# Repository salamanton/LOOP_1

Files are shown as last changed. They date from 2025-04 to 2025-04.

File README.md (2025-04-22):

# LOOP_1
Step-by-step instructions to build an open-source recordplayer, that is upgradeable, repaireable and customizable to your needs.

Loop_1 is a do-it-yourself record player. Our goal with this object is to motivate people to deal with the return to analog. Since digitalization, music has become 
increasingly accessible. Platforms such as Spotify, AppleMusic or YouTube offer us a selection that far exceeds our expectations, which means that a profound examination of the music, the albums and the artists is becoming less and less possible. In order to promote a more conscious consumption of music, Loop_1 will expand the ritual of putting on records with a record player kit to build or rebuild yourself. 
kit to build or rebuild yourself in order to continue to ensure availability for young people interested in music or for nostalgics. 
nostalgics. At the same time, the record player will be used as a trend medium to further spread the topic of open source and make makerspaces more accessible to various communities.

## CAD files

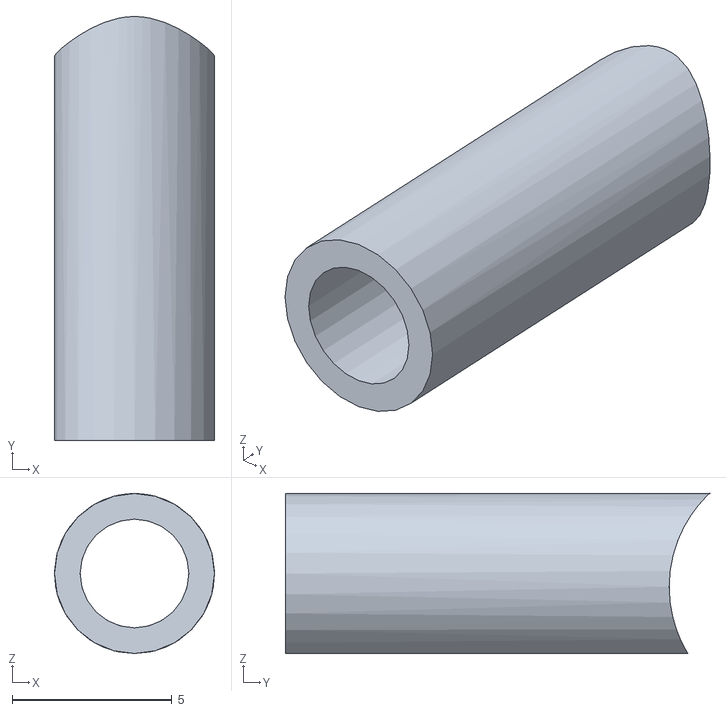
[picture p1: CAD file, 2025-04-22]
3D_Files/Distanzstück_arm_02.stl
5.00 x 13.3 x 5.00

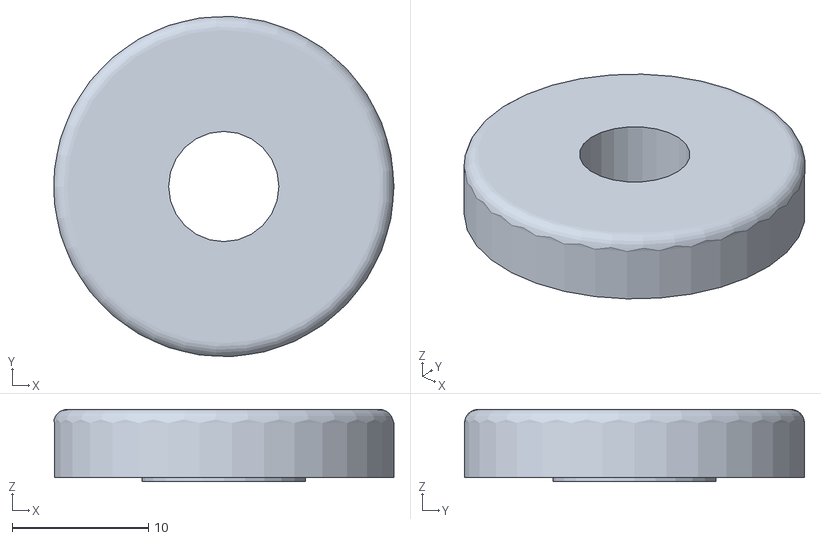
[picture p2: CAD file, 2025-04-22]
3D_Files/Anker_Abdeckung.stl
25.0 x 25.0 x 5.30

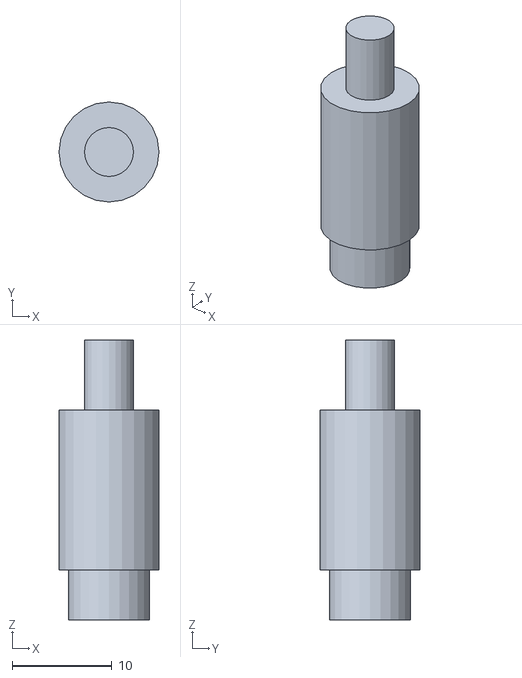
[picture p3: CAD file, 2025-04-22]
3D_Files/Distanzstück_02.stl
10.0 x 10.0 x 28.0

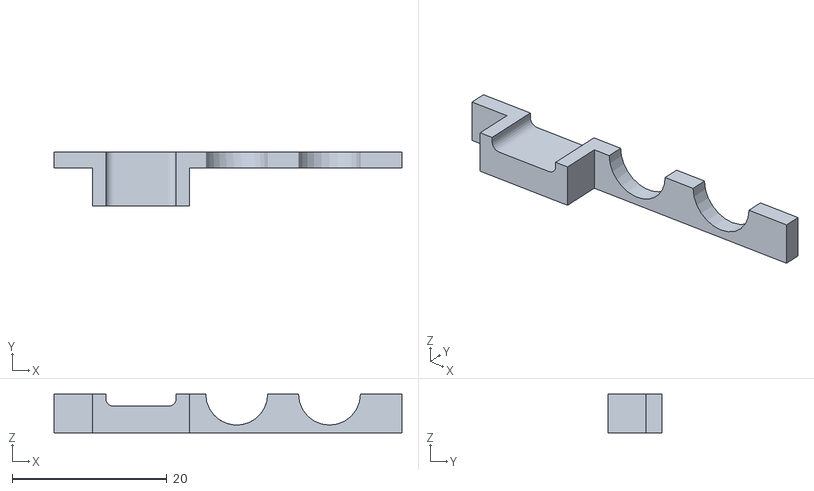
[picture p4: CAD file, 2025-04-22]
3D_Files/Ausgang_01.stl
45.0 x 7.00 x 5.00

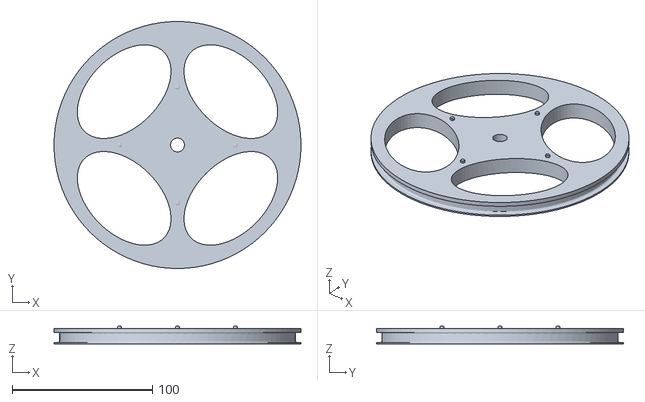
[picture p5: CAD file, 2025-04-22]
3D_Files/drehscheibe.stl
176.0 x 176.0 x 12.5

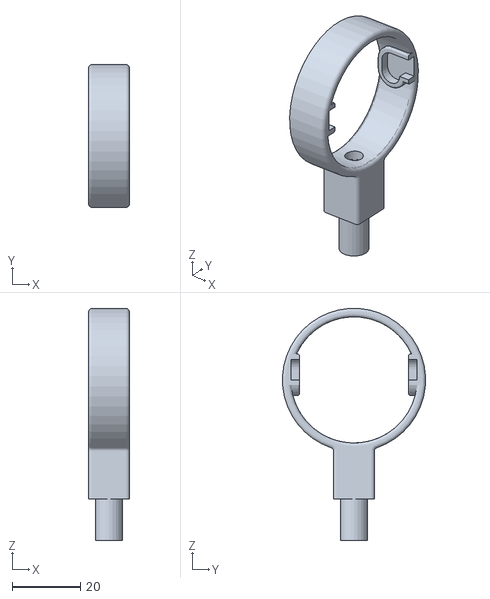
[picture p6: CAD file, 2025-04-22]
3D_Files/Anker.stl
12.0 x 41.9 x 68.0

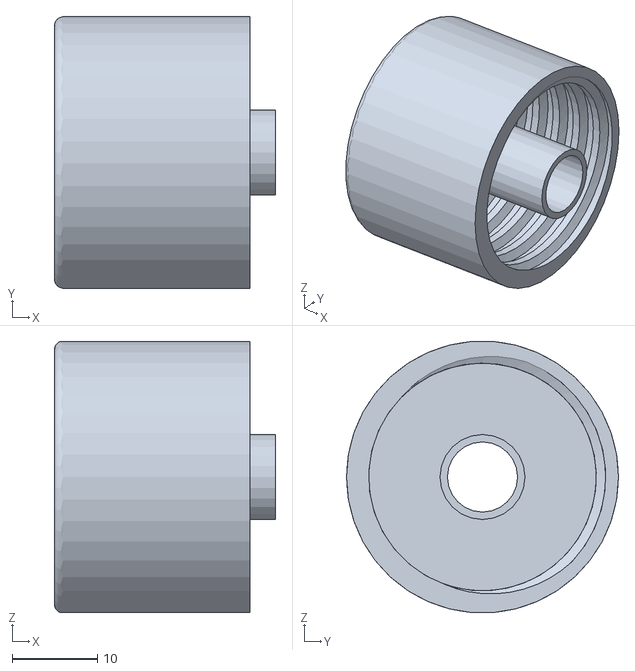
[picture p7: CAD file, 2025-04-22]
3D_Files/Gewicht_Gehäuse.stl
26.0 x 32.0 x 31.9

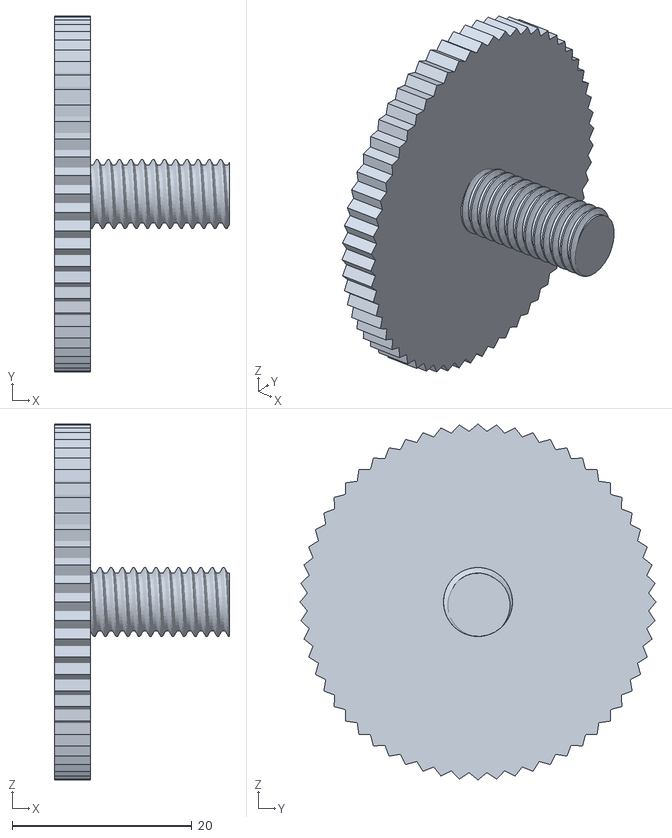
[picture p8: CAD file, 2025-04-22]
3D_Files/Stellschraube.stl
19.5 x 39.6 x 39.6

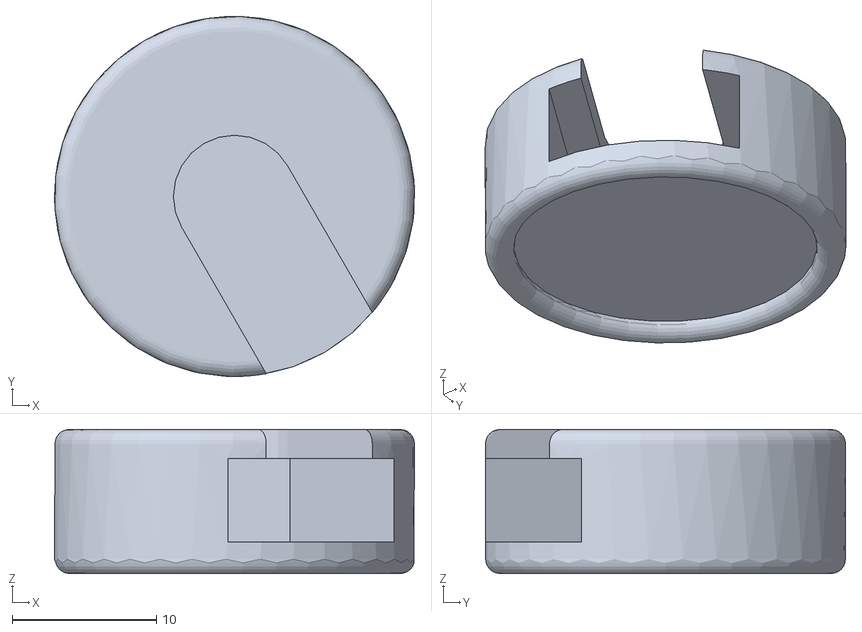
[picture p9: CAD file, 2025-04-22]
3D_Files/Fuß.stl
25.0 x 25.0 x 10.0

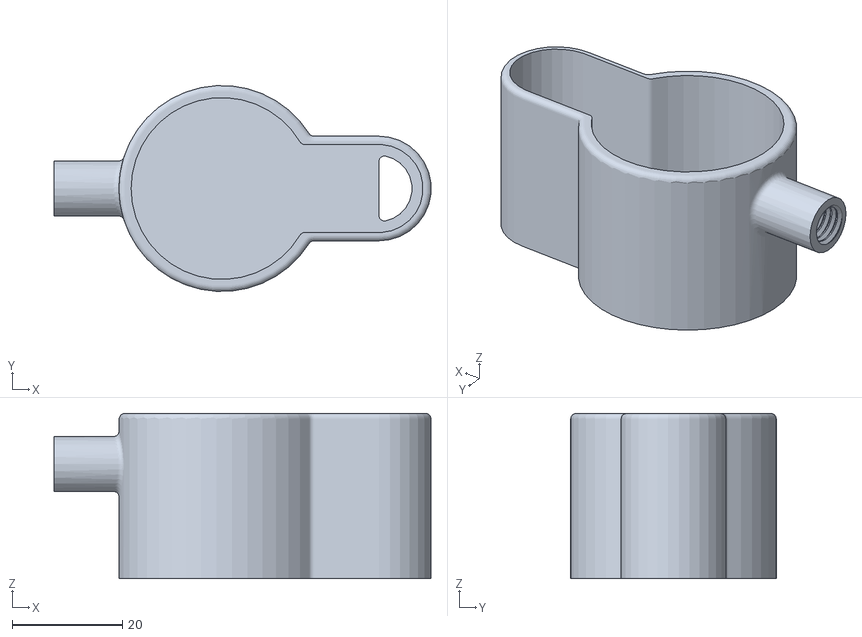
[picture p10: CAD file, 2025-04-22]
3D_Files/Schlitten.stl
68.4 x 37.3 x 30.0

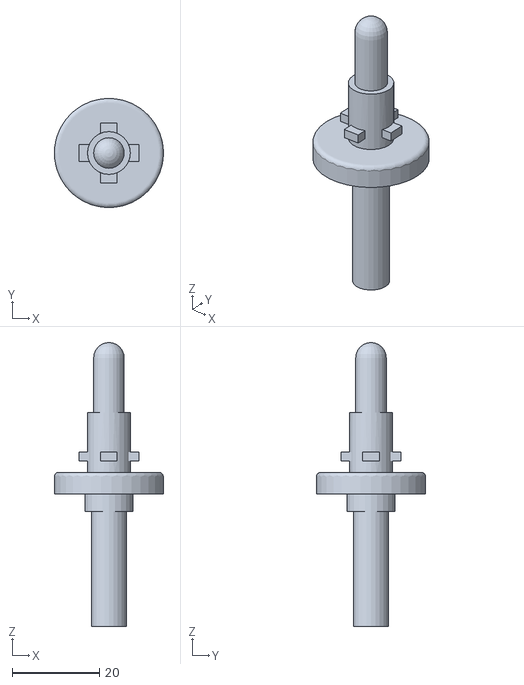
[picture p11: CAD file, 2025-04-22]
3D_Files/Achse.stl
25.0 x 25.0 x 65.0

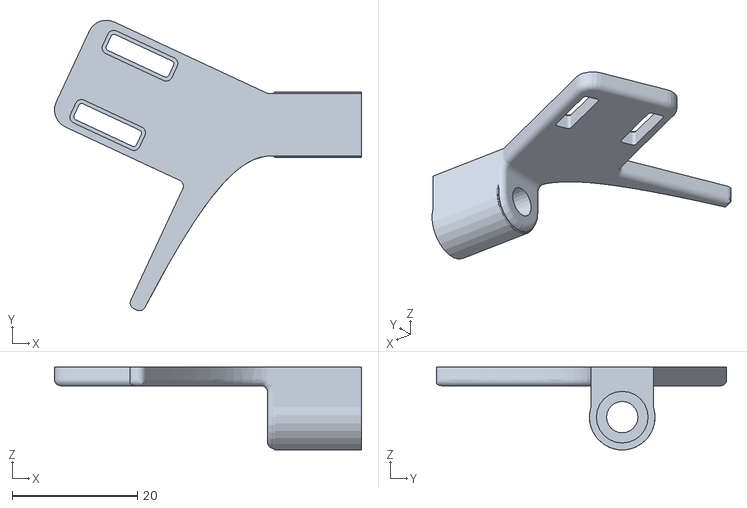
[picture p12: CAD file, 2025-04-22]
3D_Files/Tonabnehmer.stl
49.0 x 46.4 x 13.2

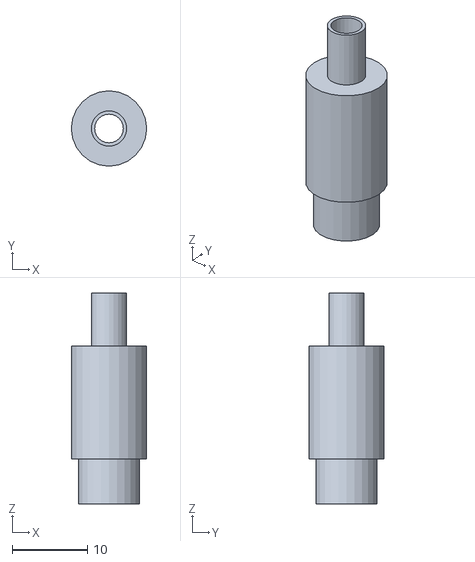
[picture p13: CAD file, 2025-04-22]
3D_Files/Distanzstück_01.stl
10.0 x 10.0 x 28.0

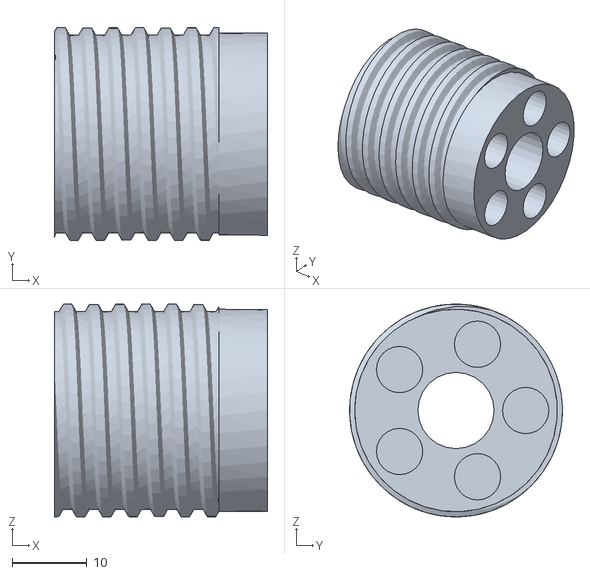
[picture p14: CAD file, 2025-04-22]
3D_Files/Gewicht_Halter.stl
28.5 x 28.5 x 28.5

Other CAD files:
3D_Files/Ausgang_02.stl
3D_Files/Distanzstück_arm_01.stl

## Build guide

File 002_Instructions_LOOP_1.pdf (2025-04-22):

# LOOP-1

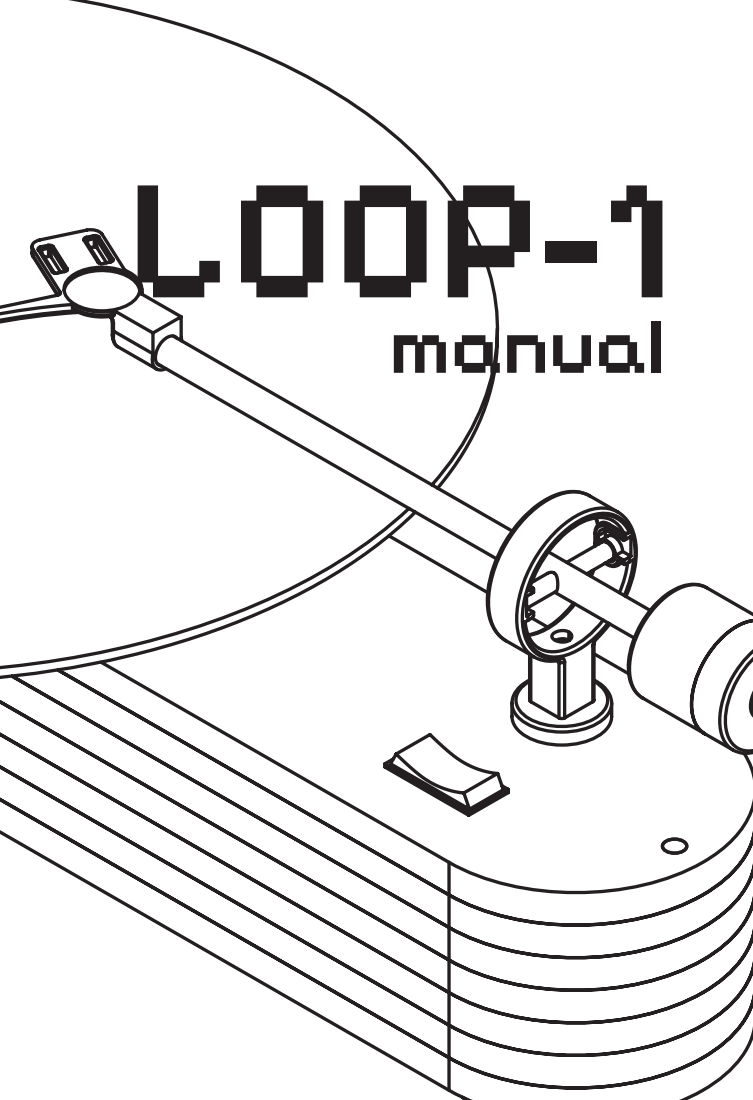
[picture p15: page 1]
manual

## Bill of materials

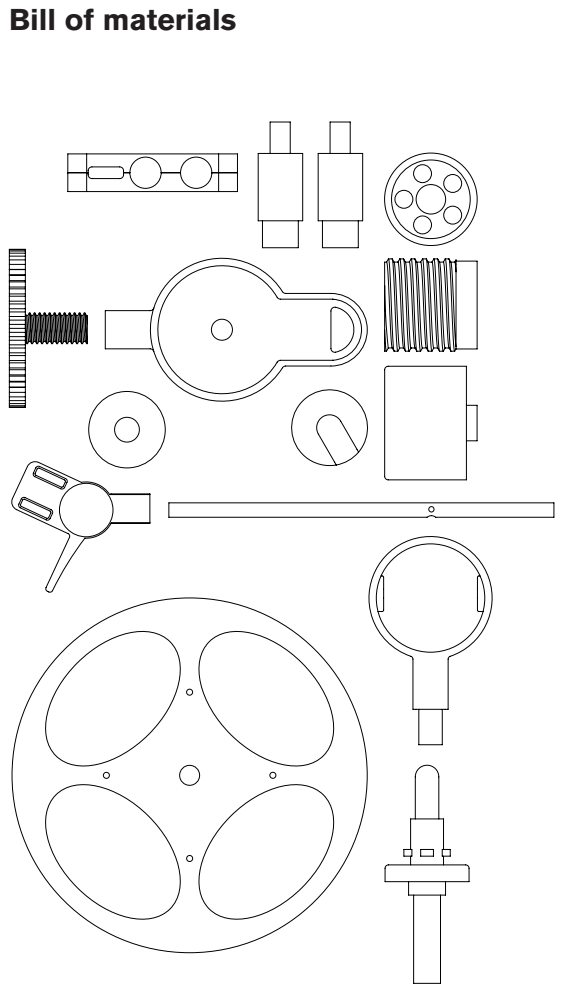
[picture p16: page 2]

Schrauben | Anzahl
M1 *4 | 8
M8 *20 | 4
Elektronik
Arduino Uno | 1
Motortreiber L298N | 1
Mini Breadboard | 1
Jumper Wire | 14
Cartridge Wire | 2
Phono Out | 2
Usb-C Port | 1
3-Positionen Kippschalter | 1
Phono Motor | 1
Spezial Komponenten
Kugellager 22mm | 4
Kugellager 6mm | 2
Stahlstab 30x3mm | 1
Stahlstab 70x6mm | 2
Stahlstab (Gewicht) 30x6mm | 5
Andere Komponenten
Riemen 300mm | 1
Filzgleiter 20mm | 4

## Schritt 1:

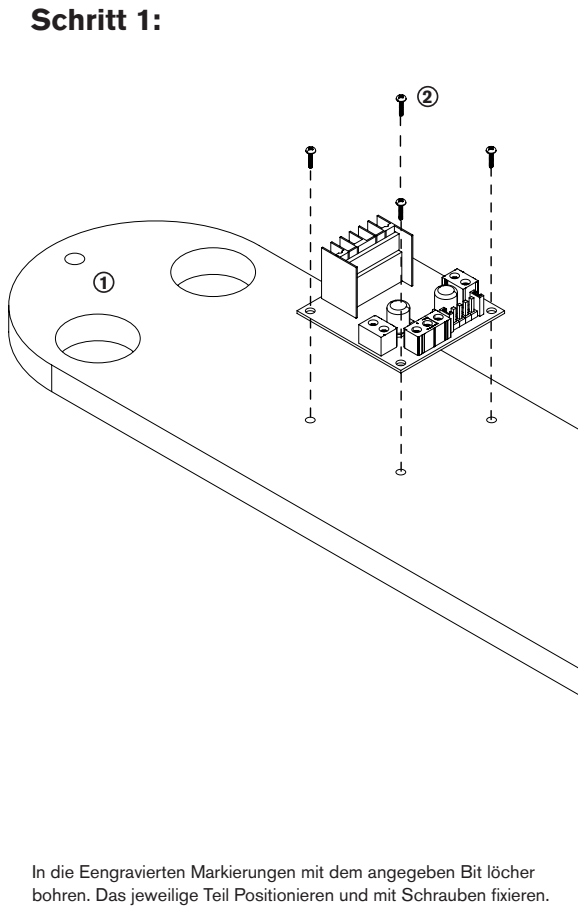
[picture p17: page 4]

In die Eengravierten Markierungen mit dem angegeben Bit löcher
bohren. Das jeweilige Teil Positionieren und mit Schrauben fixieren.

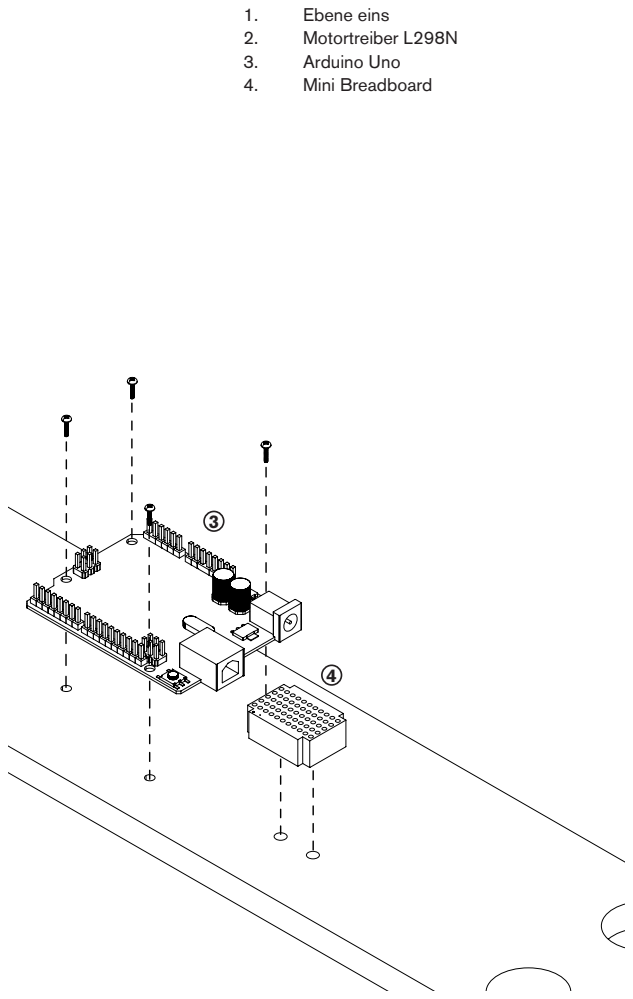
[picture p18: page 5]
1. Ebene eins 2. Motortreiber L298N 3. Arduino Uno 4. Mini Breadboard

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
## Schritt 1.1:

Nachdem die Elektronik Komponenten auf der Grundplatte fixiert wurden können die Einzelteile nun miteinander verkabelt werden (Siehe Bild rechts). Der Motor, sowie der Schalter werden erst im späteren verlauf verbaut, die können erstmal beiseite gestellt werden oder später an die verkabelung angeschlossen werden.

1. Arduino Uno
2. Motortreiber L298N
3. Plattenspieler Motor
4. USB-C Ausgang
5. Mini Breadboard
6. 3-Positionen Wippschalter

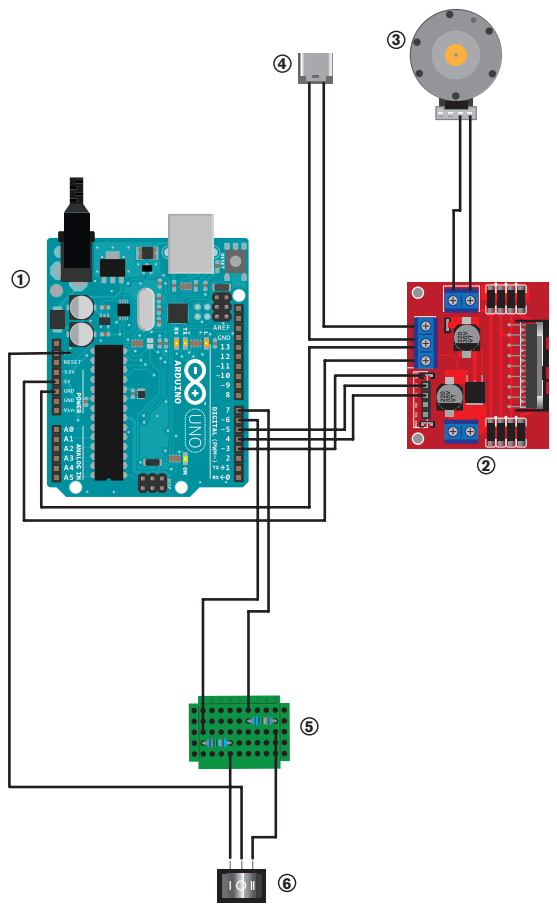
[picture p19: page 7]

## Schritt 2:

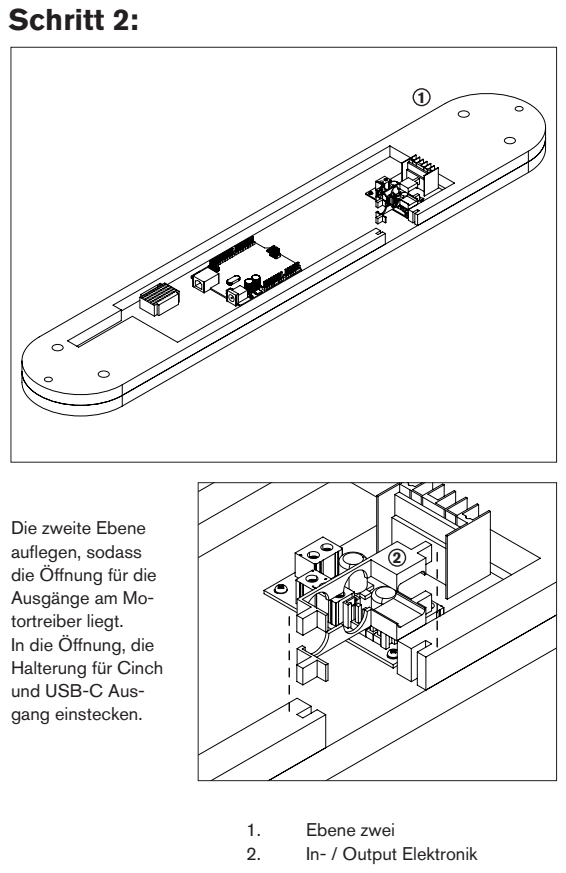
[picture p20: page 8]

Die zweite Ebene
auflegen, sodass
die Öffnung für die
Ausgänge am Mo-
tortreiber liegt.
In die Öffnung, die
Halterung für Cinch
und USB-C Aus-
gang einstecken.

1. Ebene zwei
2. In- / Output Elektronik

## Schritt 3:

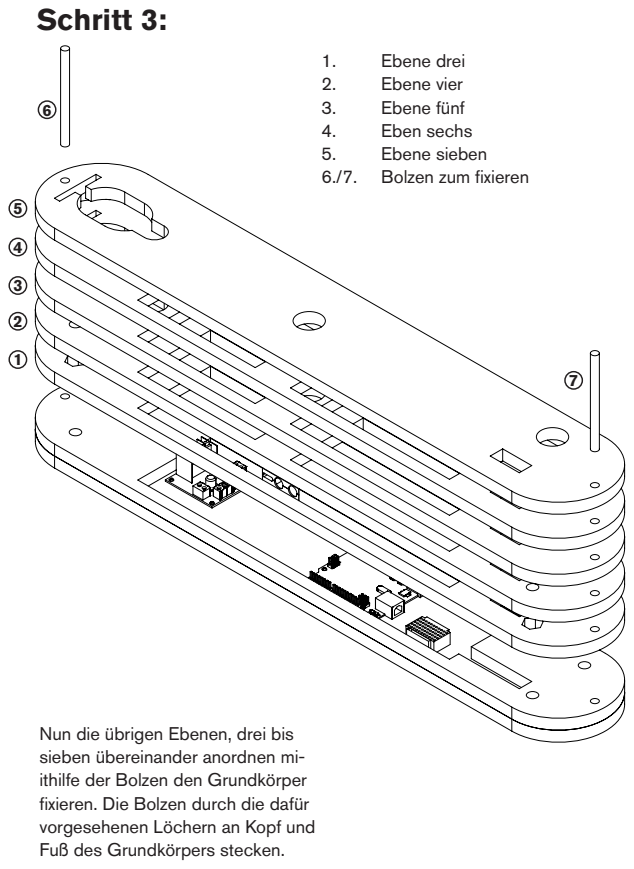
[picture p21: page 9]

1. Ebene drei
2. Ebene vier
3. Ebene fünf
4. Eben sechs
5. Ebene sieben
6./7. Bolzen zum fixieren

Nun die übrigen Ebenen, drei bis
sieben übereinander anordnen mi-
ithilfe der Bolzen den Grundkörper
fixieren. Die Bolzen durch die dafür
vorgesehenen Löchern an Kopf und
Fuß des Grundkörpers stecken.

## Schritt 4:

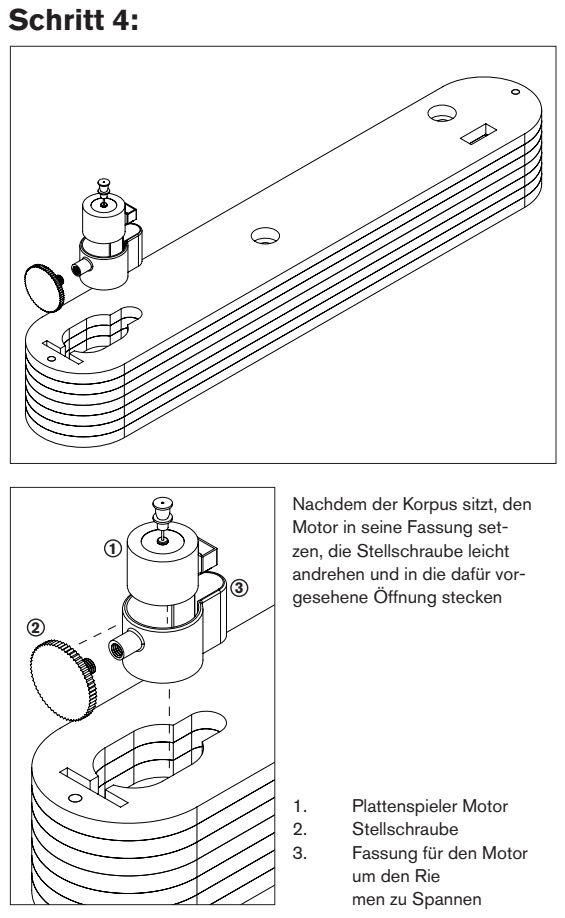
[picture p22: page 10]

Nachdem der Korpus sitzt, den
Motor in seine Fassung set-
zen, die Stellschraube leicht
andrehen und in die dafür vor-
gesehene Öffnung stecken

1. Plattenspieler Motor
2. Stellschraube
3. Fassung für den Motor
um den Rie
men zu Spannen

## Schritt 5:

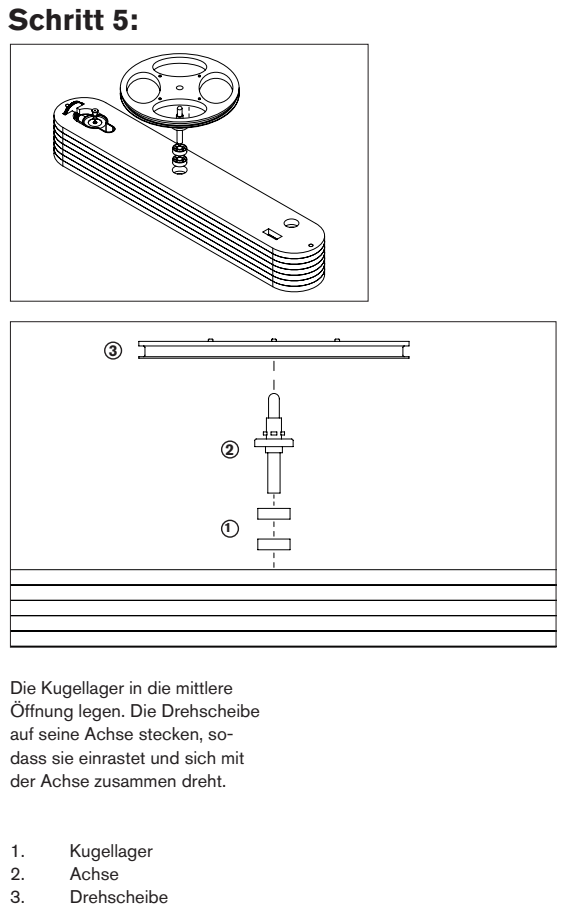
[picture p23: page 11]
1. Kugellager 2. Achse 3. Drehscheibe

Die Kugellager in die mittlere
Öffnung legen. Die Drehscheibe
auf seine Achse stecken, so-
dass sie einrastet und sich mit
der Achse zusammen dreht.

## Schritt 6:

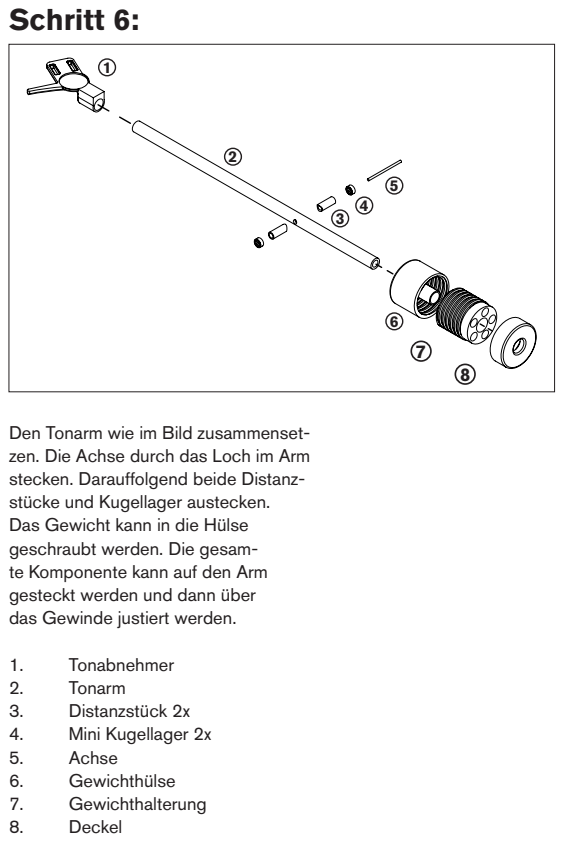
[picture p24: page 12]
1. Tonabnehmer 2. Tonarm 3. Distanzstück 2x 4. Mini Kugellager 2x 5. Achse 6. Gewichthülse 7. Gewichthalterung 8. Deckel

Den Tonarm wie im Bild zusammenset-
zen. Die Achse durch das Loch im Arm
stecken. Darauffolgend beide Distanz-
stücke und Kugellager austecken.
Das Gewicht kann in die Hülse
geschraubt werden. Die gesam-
te Komponente kann auf den Arm
gesteckt werden und dann über
das Gewinde justiert werden.

## Schritt 6.1:

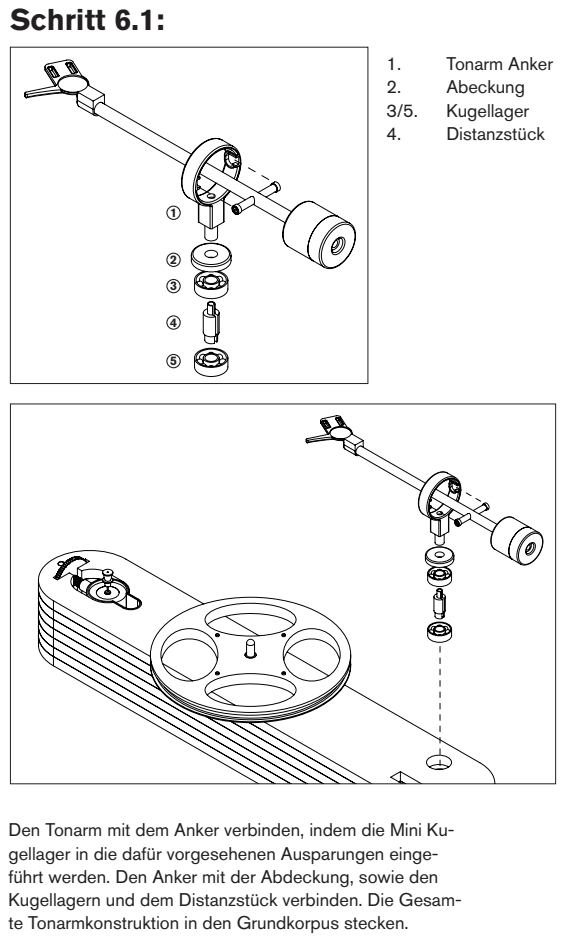
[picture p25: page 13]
1. Tonarm Anker 2. Abeckung; Kugellager; 4. Distanzstück

Den Tonarm mit dem Anker verbinden, indem die Mini Ku-
gellager in die dafür vorgesehenen Ausparungen einge-
führt werden. Den Anker mit der Abdeckung, sowie den
Kugellagern und dem Distanzstück verbinden. Die Gesam-
te Tonarmkonstruktion in den Grundkorpus stecken.

## Schritt 7:

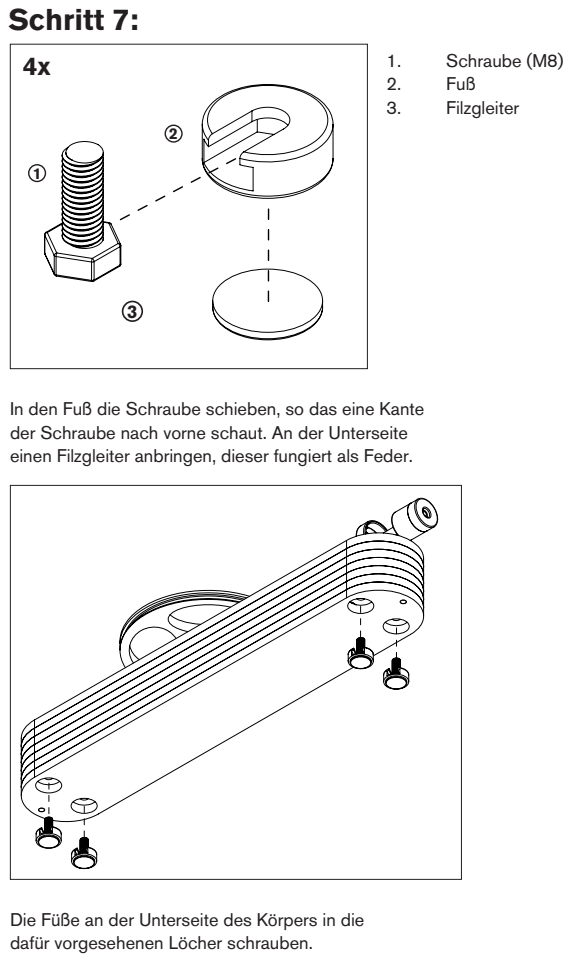
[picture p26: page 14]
Schraube (M8); 2. Fuß 3. Filzgleiter

In den Fuß die Schraube schieben, so das eine Kante
der Schraube nach vorne schaut. An der Unterseite
einen Filzgleiter anbringen, dieser fungiert als Feder.

Die Füße an der Unterseite des Körpers in die
dafür vorgesehenen Löcher schrauben.

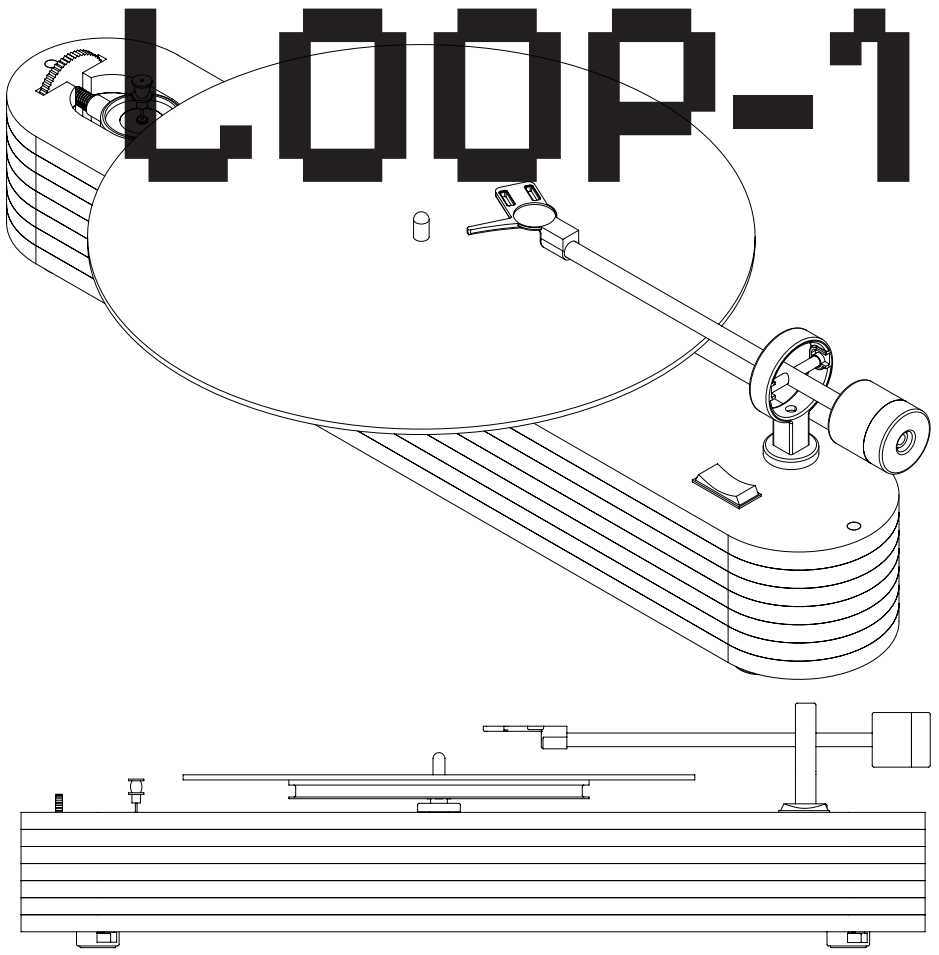
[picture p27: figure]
LOOP-1

Der Schallplattenspieler kann nun an den Strom geschlossen weden. Bei Unebenheiten oder leichten Verzerrungen können Feinjustierungen getroffen werden. An der Stellschraube lässt sich der Riemen spannen, das Gewicht lässt sich rausdrehen um den Druck auf die Platte zu erhöhen oder zu mindern und die Füße können raus oder reingedreht werden, da der Schallplattenspieler möglichst gerade stehen sollte.

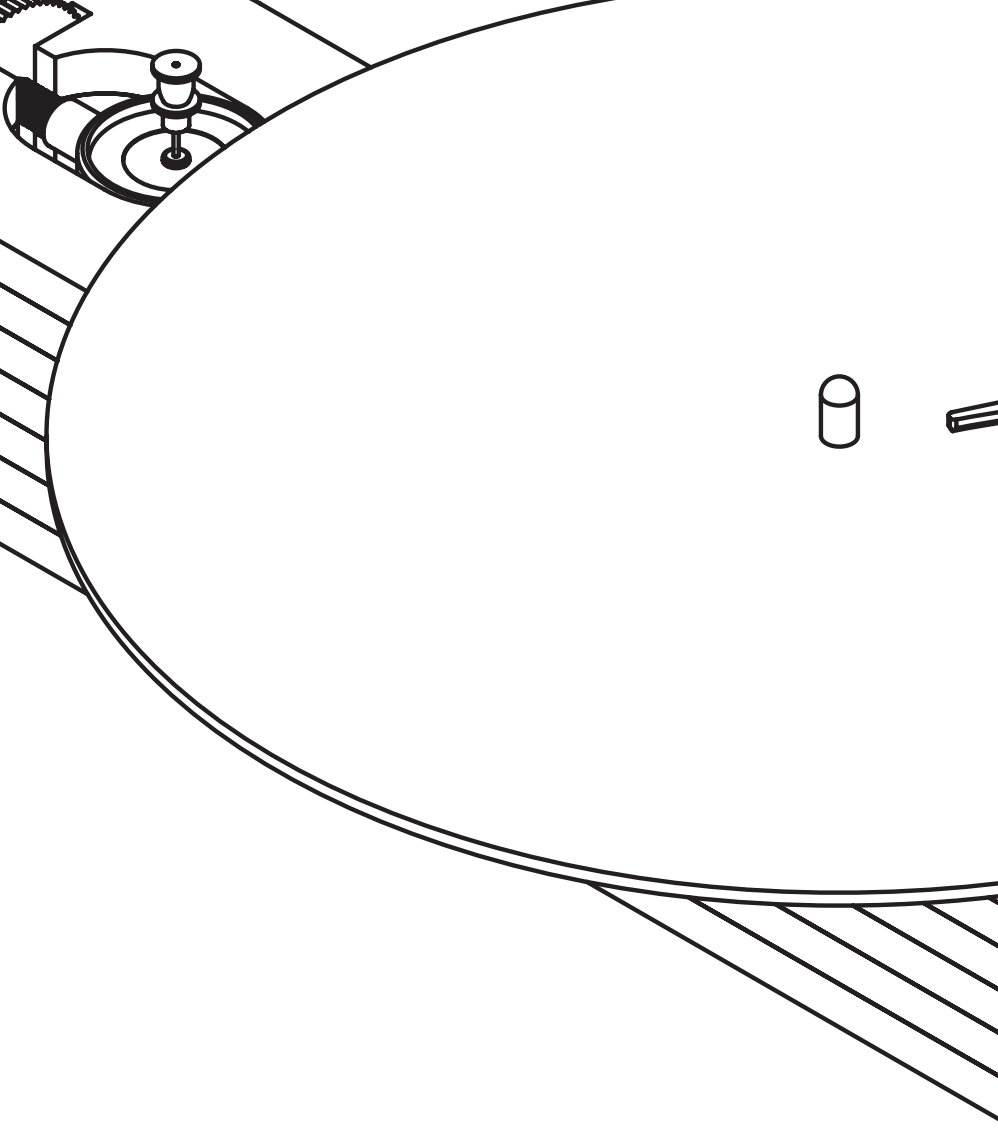
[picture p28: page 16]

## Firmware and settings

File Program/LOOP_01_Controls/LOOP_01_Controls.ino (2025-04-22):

// Pins
#define PWM_PIN 3      // PWM-Ausgang für Motor
#define IN1_PIN 4      // Richtungspin 1
#define IN2_PIN 5      // Richtungspin 2
#define SWITCH_POS1 6  // Wippschalter Position 1
#define SWITCH_POS2 7  // Wippschalter Position 2

// Drehzahlen (PWM-Werte)
#define SPEED_POSITION1 1000  // Drehzahl für Position 1 (33 1/3 RPM)
#define SPEED_POSITION2 1364  // Drehzahl für Position 2 (45 RPM)

void setup() {
  // Motortreiber-Pins
  pinMode(PWM_PIN, OUTPUT);
  pinMode(IN1_PIN, OUTPUT);
  pinMode(IN2_PIN, OUTPUT);

  // Schalter-Pins
  pinMode(SWITCH_POS1, INPUT);
  pinMode(SWITCH_POS2, INPUT);

  // Standard: Motor aus
  digitalWrite(IN1_PIN, LOW);
  digitalWrite(IN2_PIN, LOW);
}

void loop() {
  // Schalter abfragen
  bool pos1 = digitalRead(SWITCH_POS1);  // Schalterstellung 1
  bool pos2 = digitalRead(SWITCH_POS2);  // Schalterstellung 2

  // Motorsteuerung basierend auf Schalterstellung
  if (pos1 && !pos2) {
    // Position 1: Motor mit SPEED_POSITION1 in entgegengesetzter Richtung
    analogWrite(PWM_PIN, SPEED_POSITION1);
    digitalWrite(IN1_PIN, LOW);
    digitalWrite(IN2_PIN, HIGH);
  } else if (pos2 && !pos1) {
    // Position 2: Motor mit SPEED_POSITION2 in entgegengesetzter Richtung
    analogWrite(PWM_PIN, SPEED_POSITION2);
    digitalWrite(IN1_PIN, LOW);
    digitalWrite(IN2_PIN, HIGH);
  } else {
    // Position 0: Motor aus
    analogWrite(PWM_PIN, 0);
    digitalWrite(IN1_PIN, LOW);
    digitalWrite(IN2_PIN, LOW);
  }
}
